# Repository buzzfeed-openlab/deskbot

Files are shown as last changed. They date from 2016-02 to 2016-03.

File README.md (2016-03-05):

# deskbot: How to add presets and automations to your BuzzFeed SF standing desk

The code in this repo is drawn from TJ Hunter's very great [photon-desk repo](https://github.com/Hypnopompia/photon-desk) which tells you how to convert your [V3 GeekDesk](http://www.geekdesk.com/geekdesk-v3-frame-only) into a desk with pre-sets. He even has [nifty controllers you can order](https://www.tindie.com/products/TJ_Hunter/photon-geekdesk-controller/) but this one just uses a [Photon](https://docs.particle.io/datasheets/photon-datasheet/) and [Photon Relay Shield](https://docs.particle.io/datasheets/photon-shields/#relay-shield) that you can buy from [the Particle store](http://store.particle.io). We're also going to show you how to use IFTTT to hook your desk pre-sets up to your phone.

You will need:

**Hardware**
- Photon
- Photon Relay Shield
- Ultrasonic ping sesnor, like [this one](http://www.amazon.com/SainSmart-HC-SR04-Ranging-Detector-Distance/dp/B004U8TOE6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)
- 4 Male-to-Female jumper wires
- USB-to-micro-USB cable, preferably pretty long
- Outlet USB brick (optional)
- 3D printed case for the deskbot
- Long screws (like 3 inches)
- Your standing desk

**Software**
- A [Particle Build](http://build.particle.io) account
- An [IFTTT](https://ifttt.com) account
- The [IFTTT "Do" app](https://ifttt.com/products/do/button)
- A Google account with Google Calendar

## Step 1: Start Printing This Thing

First, print the 3D case for the deskbot. The `.stl` file is in this repo. We used a MakerBot M2 with PLA filament.

## Step 2: Claim Your Photon

You're going to need to unbox your Particle Photon and claim it to the Particle Build account you made. Info on how to do that is [here](https://docs.particle.io/guide/getting-started/start/photon/#connect-your-photon).

## Step 3: Add Code

Copy the text of deskbot.ino into a new app called "deskbot" in Particle Build. Then go to the libraries button (bookmark in the lower left corner) and add the RelayShield library to the deskbot app. This will automatically add a new line of code at the top of your file-- that's good! Save your app, make sure your Photon is plugged in and online, and hit the lightning bolt to flash the code to your Photon. The RGB LED will be purple for a little while (especially if it is the first time you're flashing code to this device), and then it will flash green, then cyan again.

## Step 4: Assembly

Is your case done printing? Good! Time for assembly.

(NOTE: Depending on the width of your screws, you might need to widen the holes on the Relay Shield using a drill press. If you work at BuzzFeed SF, ask one of the OpenLab Fellows for help with this.)

Reference the awesome post we have on this to see how to put it all together. Basically, you line up the first two relays with the holes. Make sure you unplug your desk (that's super important) before plugging anything from your desk into the relay shield. The order is roughly:

1) Plug the Photon into the Relay Shield, being careful to line up the Photon with the outline on the shield.

2) Use the jumper wires to connect the ping sensor to the headers on either side of the Photon. You should connect:

`Vcc` to `VIN`

`Trig` to `D1`

`Echo` to `D2`

`Gnd` to `GND`

I looped the wires underneath the Photon to make it a bit cleaner. You can do this if you want, or just squish them into the box later.

3) Plug in the micro-USB cable to the micro-USB port on your Photon.

4) UNPLUG YOUR DESK FROM THE WALL. I cannot stress this enough.

5) Unscrew the black controller from your desk and open it up. You'll see a particular arrangement of wires in there. This is sort of a crazy arrangement, just take my word for it and wire it like this:

```
|   |   |       |   |   |
bw      yw      bw      yw
+   -               -   +
```

6) Flip the whole relay over and put it in the bottom part of the deskbot case. You can wrap the ping sensor around the back of the relay shield so that it is technically above the shield, facing downward into the two large holes exposing its sensors. Center the wires in the exit tracts cut in front of relays 1 and 2 and close the box.

## Step 5: Turn it on and test it!
Set the box on your desk with the ping sensor facing down and pointing towards the ground, off the edge of your desk. This is how your deskbot "sees," so make sure there isn't anything obscuring its view of the floor.

Plug the USB cable into your power brick or into your computer. This will turn on your deskbot.
If you have the Particle CLI, you can test this quickly by using the command `particle call [NAME OF YOUR DEVICE] set 90` to make it raise up to about 90 cm.

I guess if you don't have the CLI, wellllll.... if I really loved you I'd have some code here you could use to test it. But I don't love you that much, so just make an IFTTT account and see if you can get it working that way.

## Step 6: Making an IFTTT DO recipe

Follow the steps on the IFTTT DO app to create a recipe for Particle. You'll need to authenticate your Particle account with the same email and password you used for Particle Build. Once this is done, tell IFTTT you want it to use your recipe to call a function. The fuction is "set" and the data the desired height of your desk in centimeters. Mine is 65 for sitting and 95 for standing. You can adjust yours as necessary. Make one recipe for sitting and one for standing. When you press the button, your desk should go to the desired height!

## Step 7: Google Calendar

Create a Google Calendar called "deskbot" or "standing desk" or something. It doesn't matter, as long as you can recognize it. Go into your IFTTT account through the web interface and create a recipe with Google Calendar as the trigger. What I like to do here is hook up the deskbot calendar to IFTTT and have it trigger the Particle function "set" with data "95" when it encounters an event with the word "up" in it. Similarly, it triggers "set" with the data "65" when it encounters an event with the word "down." Now you can schedule the ups and downs of your desk!

## Step 8: Attach to Desk

Screw the box into your desk, with the ping sensor facing down. Make sure that the ping sensor isn't blocked by anything. Enjoy.

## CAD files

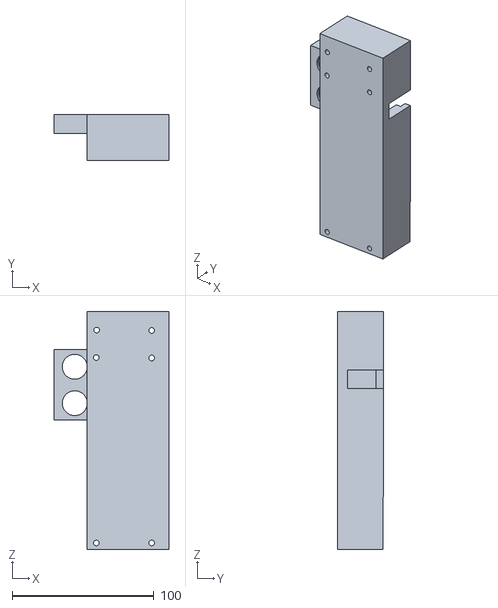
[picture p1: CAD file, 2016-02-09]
deskbot-case/deskbot-bottom.stl
81.2 x 32.3 x 168.0

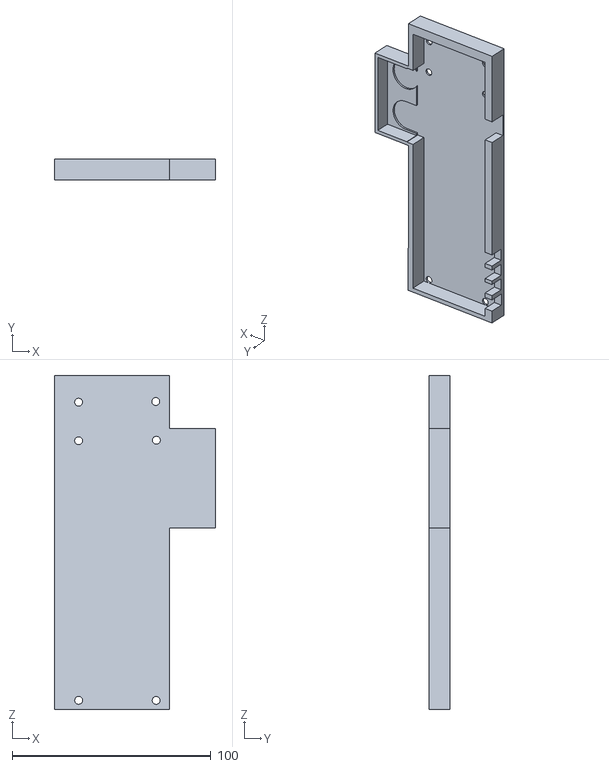
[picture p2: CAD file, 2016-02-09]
deskbot-case/deskbot-top.stl
81.2 x 10.8 x 168.0

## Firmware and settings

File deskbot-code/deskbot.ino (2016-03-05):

// Adapted from TJ Hunter's code, found at https://github.com/Hypnopompia/photon-desk
// The basic difference here is that we made it work with a Particle relay shield instead of his custom board
// TJ's boards are customized for GeekDesks and are very great.

RelayShield myRelays;

int trigPin = D1;
int echoPin = D2;

uint32_t lastCm, targetCm;
bool movingUp, movingDown;
uint32_t readings[10];
uint32_t readingIndex = 0;
unsigned long lastPingTime = 0;    // When we're not moving, we want to ping once per second to watch for manual movement.
unsigned long lastPublishTime = 0; // Keep track of when we last published and event so we don't flood
unsigned long movingStartTime;     // Keep track of when we started moving so we can timeout
unsigned long movingTimeOut = 0;   // # of seconds; Stop trying to move after moving for this many seconds in case something bad happens
unsigned long deskSpeed = 3;       // 3cm per second
char publishString[40];

void setup() {
  myRelays.begin(1);
	Particle.function("get", getHeight);
	Particle.function("set", setHeight);
  Particle.function("go",relayGo);
	// Initialize the HC-SR04
	pinMode(trigPin, OUTPUT);
	digitalWriteFast(trigPin, LOW);
	stop();
	delay(50);
	Serial.begin(115200);
}

void loop() {
	uint32_t currentHeight;
	// Timeout Check
	if ( (movingUp || movingDown) && ( (millis() - movingStartTime) / 1000 >= movingTimeOut ) ) {
		stop();
	}
	// Target height check
	if (movingUp || movingDown) {
		currentHeight = microsecondsToCentimeters(readPingSensor());
		if (currentHeight != 0) { // we got a valid reading
			// The desk takes about a cm to come to a full stop, so stop 1cm early
			if ( (movingUp   && currentHeight >= ( targetCm - 1) ) ||
			     (movingDown && currentHeight <= ( targetCm + 3) )
			) { // We've reached our target height. Stop everything!
				stop();
			}
		}
	}
	// When we're not moving, we want to ping once per second to watch for manual movement.
	if ( (!movingUp && !movingDown) && (millis() - lastPingTime > 1100) ) {
		readPingSensor();
		lastPingTime = millis();
	}
}

int relayGo(String command){
    // Ritual incantation to convert String into Int
    char inputStr[64];
    command.toCharArray(inputStr,64);
    int i = atoi(inputStr);
    // Turn the desired relay on
    myRelays.on(i);
    delay(500);
    myRelays.off(i);
    // Respond
    return 1;
}

int relayOn(String command){
    // Ritual incantation to convert String into Int
    char inputStr[64];
    command.toCharArray(inputStr,64);
    int i = atoi(inputStr);
    // Turn the desired relay on
    myRelays.on(i);
    // Respond
    return 1;
}

int relayOff(String command){
    // Ritual incantation to convert String into Int
    char inputStr[64];
    command.toCharArray(inputStr,64);
    int i = atoi(inputStr);
    // Turn the desired relay off
    myRelays.off(i);
    // Respond
    return 1;
}

void goUp() {
	Particle.publish("movingup", NULL, 60, PRIVATE);
	Serial.print("Going up to ");
	Serial.println(targetCm);
	stop();
	myRelays.on(1);
	movingUp = true;
	movingStartTime = millis();
}

void goDown() {
	Particle.publish("movingdown", NULL, 60, PRIVATE);
	Serial.print("Going down to ");
	Serial.println(targetCm);
	stop();
	myRelays.on(2);
	movingDown = true;
	movingStartTime = millis();
}

void stop() {
	myRelays.off(1);
	myRelays.off(2);
	movingUp = false;
	movingDown = false;
}

uint32_t getHeight(String command) {
	lastCm = 0; // Force a debug print to Serial
	return microsecondsToCentimeters(readPingSensor());
}

int setHeight(String command) {
	uint32_t currentHeight = microsecondsToCentimeters(readPingSensor());
	targetCm = command.toInt();
	if (currentHeight == targetCm) {
		Serial.println("Target and current heights are the same.");
	} else {
		// Calculate the distance we need to travel and using the known
		// travel speed of the desk, set a more appropriate timeout rather than hardcoding it.
		if (currentHeight > targetCm) {
			movingTimeOut = (currentHeight - targetCm) / deskSpeed;
			goDown();
		} else if (currentHeight < targetCm) {
			movingTimeOut = (targetCm - currentHeight) / deskSpeed;
			goUp();
		}
		movingTimeOut += 2; // It takes a bit to get up to speed
		Serial.print("Timeout in ");
		Serial.print(movingTimeOut);
		Serial.println(" seconds.");
	}
	return 1;
}

uint32_t avgReading() {
	uint32_t sum = 0, nonZero = 0, avg = 0;;
	for (uint32_t i = 0; i < 10; i++) {
		if (readings[i] > 0) nonZero++;
		sum += readings[i];
	}
	if (sum > 0 && nonZero > 0) {
		avg = sum / nonZero;
	}
	return avg;
}

uint32_t readPingSensor() {
	uint32_t duration, trycount, cm, avg;
	uint32_t haveGoodReading = 0;
	uint32_t readingThreshold = 58 * 4; // about 4cm
	trycount = 0;
	do {
		duration = ping();
		cm = microsecondsToCentimeters(duration);
		// less than 54cm or more than 120cm is likely an error.
		if (cm >= 54 && cm <= 120) {
			readings[readingIndex++] = duration;
			if (readingIndex >= 10) readingIndex = 0;
			// Do some smoothing on the readings to throw out outliers.
			avg = avgReading();
			// A reading more than 4cm from the average is probably also a bad reading.
			if (avg == 0 || abs(duration - avg) < readingThreshold ) {
				haveGoodReading = 1;
				Serial.print(".");
			} else {
				delay(50);
				Serial.print("o");
			}
		} else {
			delay(50);
			Serial.print("x");
		}
	} while ( ( !haveGoodReading ) && trycount++ < 25);
	Serial.print("  ");
	if (haveGoodReading == 0) {
		Serial.print("Bad reading. Avg: ");
		Serial.print(avg);
		Serial.print(" Reading: ");
		Serial.println(duration);
		duration = 0;
		cm = 0;
	} else {
		Serial.print(cm);
		Serial.print("cm, ");
		Serial.print(duration);
		Serial.println("us");
	}
	sprintf(publishString, "%d", cm);
	if ( (movingUp || movingDown) && (millis() - lastPublishTime > 1000) ) {
		Particle.publish("height", publishString, 60, PRIVATE);
		lastPublishTime = millis();
	}
	/* Debugging output */
	if (cm != lastCm) {
		lastCm = cm;
		if ( (millis() - lastPublishTime > 1000) ) {
			Particle.publish("height", publishString, 60, PRIVATE);
			lastPublishTime = millis();
		}
	}
	return duration;
}

uint32_t ping() {
	uint32_t duration;
	pinMode(echoPin, INPUT);
	pinMode(trigPin, OUTPUT);
	// The sensor is triggered by a HIGH pulse of 10 or more microseconds.
	digitalWriteFast(trigPin, HIGH);
	delayMicroseconds(10);
	digitalWriteFast(trigPin, LOW);
	duration = pulseIn(echoPin, HIGH); // Time in microseconds to recieve a ping back on the echo pin
	return duration;
}

uint32_t microsecondsToInches(uint32_t microseconds)
{
  // According to Parallax's datasheet for the PING))), there are
  // 73.746 microseconds per inch (i.e. sound travels at 1130 feet per
  // second).  This gives the distance travelled by the ping, outbound
  // and return, so we divide by 2 to get the distance of the obstacle.
  // See: http://www.parallax.com/dl/docs/prod/acc/28015-PING-v1.3.pdf
  return microseconds / 74 / 2;
}

uint32_t microsecondsToCentimeters(uint32_t microseconds)
{
  // The speed of sound is 340 m/s or 29 microseconds per centimeter.
  // The ping travels out and back, so to find the distance of the
  // object we take half of the distance travelled.
  return microseconds / 29 / 2;
}

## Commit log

2016-02-09 added info
    [deskbot-bottom.stl, deskbot-top.stl]
2016-03-05 Update deskbot.ino
    switched up and down relays (up is 1 and down is 2)
